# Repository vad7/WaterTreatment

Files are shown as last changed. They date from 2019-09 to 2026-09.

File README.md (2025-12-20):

# Контроллер водоподготовки и водоснабжения
Для контроллера используется плата Arduino DUE или Arduino DUE Core (ARM SAM3x8e).<br>

Также, как минимум, нужны платы: реле, часов DS3231 + EEPROM, сети на W5500.<br>
Детальное описание: http://vad-7.blogspot.com/2019/12/blog-post.html <br>
<br>
Возможности (версия 1.1.72):<br>
* Управление дозатором реагента по расходу
* Промывка двух фильтров (например - обезжелезивателя, умягчителя) по времени и по расходу<br>
* Управление насосной станцией по датчику давления воды, защита от перегрузки и сухого хода<br>
* Глубокий контроль рабочего состояния системы
* Графический веб-интерфейс с поддержкой мобильных устройств<br>
* Текстовый дисплей LCD2004, кнопки управления<br>
* Расширенная статистика с записью на SD карту<br>
* Оповещения о сбоях через email или sms.<br>
* Modbus RTU - Счетчик электричества (PZEM-004Tv3/PZEM-0xx), платы Реле. Автовыбор портов 1-3<br>
* Весы на плате HX711 для контроля уровня реагента<br>
* Аналоговый датчик уровня воды 4-20 mA<br>
* Датчик температуры DS18B20 или NTC<br>
* Контроль протечек (датчики XKC-Y25), затопления (датчики типа поплавок), переполнения бака<br>
* Контроль работы дренажного насоса (вторая шина Modbus-RTU), с возможностью отключения через Modbus реле, защита от сухого хода и перегрузки<br>
* Возможность подключения счетчика питьевого фильтра (обратного осмоса)<br>
* Управление подогревом септика<br>
* Контроль насоса откачки септика, реле насоса септика, возможность работы со сломаным поплавком или без поплавка<br>
* Другая автоматизация (например, вентилирование газов - радона и сероводорода, слив осадка бака)<br>
* Расширенный контроль безопасности (сухой ход и перегрузка НС, незакрытый кран, забитый инжектор и т.п.)<br>
* Датчик протока (FS-K2) фильтра питевой воды (обратный осмос), поддержка повышенного давления воды при заполнении ОС фильтра
* Таймеры (ежесуточные и периодические), включение обычных реле и Modbus

<br>

Схема
Схема_2
Датчики
Плата

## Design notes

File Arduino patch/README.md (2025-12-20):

# WaterTreatment
Файлы которые надо заменить в стандартном SDK Due (смотрите путь к файлам начиная с hardware)<br>
Папку "sam" перезаписать скорее всего куда-то сюда: "C:\Users\\%USERNAME%\AppData\Local\Arduino15\packages\arduino\hardware\\"<br>
Библиотека DUE SAM: https://github.com/arduino/ArduinoCore-sam

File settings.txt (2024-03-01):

 ------ Контроллер водоподготовки ver. 1.51  сборка Feb 17 2024 14:24:27 ------
Конфигурация: vad7: Водоснабжение, Обезжелезивание Quantum DMI-65, Дозирование хлора, Умягчение
Создание файла: 09:28:39 19.02.2024 

  1.1 Опции
 - Настройка встроенных графиков -
Период накопления графиков (сек): 10
Запись графиков на карту памяти: 1
 - Дополнительное оборудование -
Логировать обмен между беспроводными датчиками: 0
Генерация звукового сигнала: 1
На шинах 1-Wire(DS2482) только один датчик: 1 

  1.2 Сетевые настройки
Использование DHCP: 0
IP адрес контроллера: 192.168.0.8
DNS сервер: 8.8.8.8
Шлюз: 192.168.0.1
Маска подсети: 255.255.255.0
MAC адрес контроллера: DE:A1:1E:01:02:04
Запрет пинга контроллера: 0
Использование паролей: 1
Пароль пользователя (user): 
Пароль администратора (admin): q12
Проверка ping до сервера: never:0;1 min:0;5 min:0;20 min:0;60 min:1;120 min:0;
Адрес пингуемого сервера: 192.168.0.1
Ежеминутный контроль связи с Wiznet W5xxx: 1
Время очистки сокетов: never:0;10 sec:0;30 sec:1;90 sec:0;
Время сброса чипа: W5500: never:1;6 hours:0;24 hours:0;
Размер пакета для отправки в байтах: 1465
Не ожидать получения ACK при посылке следующего пакета: 0
Пауза перед отправкой следующего пакета, если нет ожидания ACK. (мсек): 10

  1.3 Настройки даты и времени
Установленная дата: 19.02.2024
Установленное время: 09:28
Адрес NTP сервера: ntp0.ntp-servers.net
Часовой пояс (часы): 3
Синхронизация времени по NTP раз в сутки: 1
Синхронизация раз в час с I2C часами: 0

  1.4 Уведомления
Сброс контроллера: 1
Возникновение ошибок: 1
Сигнал «жизни» (ежедневно в 12-00): 0
Достижение граничной температуры: 1
 Граничная температура в доме (если меньше то посылается уведомление): 2.00
Проблемы с SD картой и SPI flash: 1
Прочие уведомления: 1
 - Настройка отправки почты -
Посылать уведомления по почте: 1
Адрес smtp сервера: mail.smtp2go.com
Порт smtp сервера: 25
Необходимость авторизации на сервере: 1
Логин для входа: Arduino-DUE
Пароль для входа: ...
Адрес отправителя: ...
Адрес получателя: ...
Добавлять в уведомление информацию о состоянии: 1
 - Настройка отправки SMS -
Посылать уведомления по SMS: 0
Телефон получателя: 0.380
Сервис отправки SMS: sms.ru:1;smsc.ru:0;smsc.ua:0;smsclub.mobi:0;
Адрес сервиса отправки SMS: 0.0.0.0
API ID: api_id
none: none

  1.5 Настройка MQTT
Не поддерживается, нет в прошивке
  2.1 Датчики температуры
AIR     [28FFF949621403B1] Температура воздуха:  T=11.18, Tmin=1.00, Tmax=30.00, Terr=0.00, Ttest=12.00

  2.2 Аналоговые датчики
PWATER  Датчик давления воды:  P=2.87 Pmin=2.50 Pmax=3.80 Ptest=3.00 Zero=40 Kof=0.175 Pin=AD10
LTANK   Датчик уровня бака:  P=97.29 Pmin=5.00 Pmax=99.00 Ptest=8.90 Zero=4005 Kof=4.500 Pin=AD1

  2.3 Датчики сухой контакт
REG     Идет регенерация:  In=0 Level=0 Test=0 Pin=56 Type=
REGBW   Идет обратная промывка:  In=0 Level=0 Test=0 Pin=43 Type=
REG2    Идет регенерация умягчителя:  In=0 Level=0 Test=0 Pin=54 Type=
FLOOD   Затопление:  In=0 Level=1 Test=0 Pin=23 Type=
LEAK    Протечка:  In=0 Level=1 Test=0 Pin=24 Type=
SEPTIC  Авария септика:  In=0 Level=1 Test=0 Pin=5 Type=

  3.1 Реле
RBST1   Реле насосной станции Pin:47 Status: 0
RBST2   Реле насосной станции 2 Pin:3 Status: 0
RFEEDP  Реле включения дозирующего насоса Pin:46 Status: 0
RWON    Реле подачи воды Pin:7 Status: 1
RWOFF1  Реле отключения воды после фил.1 Pin:45 Status: 0
RSTREG  Реле старта рег. обезжелезивателя Pin:9 Status: 0
RSTREG2 Реле старта рег. умягчителя Pin:8 Status: 0
RDRAIN  Реле слива 1 Pin:44 Status: 0
RDRAIN2 Реле слива 2 Pin:6 Status: 0
RFILL   Реле заполнения бака Pin:31 Status: 0
RSILT   Реле слива отстоя бака Pin:50 Status: 0

  3.1 Реле
RBST1   Реле насосной станции Pin:47 Status: 0
RBST2   Реле насосной станции 2 Pin:3 Status: 0
RFEEDP  Реле включения дозирующего насоса Pin:46 Status: 0
RWON    Реле подачи воды Pin:7 Status: 1
RWOFF1  Реле отключения воды после фил.1 Pin:45 Status: 0
RSTREG  Реле старта рег. обезжелезивателя Pin:9 Status: 0
RSTREG2 Реле старта рег. умягчителя Pin:8 Status: 0
RDRAIN  Реле слива 1 Pin:44 Status: 0
RDRAIN2 Реле слива 2 Pin:6 Status: 0
RFILL   Реле заполнения бака Pin:31 Status: 0
RSILT   Реле слива отстоя бака Pin:50 Status: 0

  3.5. Частотные датчики потока
FLOW    Датчик протока:  Контроль мин. потока: 0, Минимальный поток (куб/ч)=0.000, Коэффициент (имп*л)=400.000, Тест (куб/ч)=0.000

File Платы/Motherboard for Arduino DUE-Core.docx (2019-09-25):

Платы 100x100мм.

Главная плата питается от 5V. Для аналогового выхода есть возможность подключить другое напряжение.

На плате места для:

1. платы часов (ZS_042)

2. платы сети W5500 lite (USR-ES1)

3. платы MicroSD 5V

4. разъем MicroSD

5. 3-х узких плат RS485 - TTL или других Serial-устройств.

6. 2 платы для датчиков температуры DS18B20 или других I2C устройств

7. дисплея LCD2004 (1602)

8. 4-х кнопок

9. Вторая шина I2C.

Входы-выходы:

1. два токовых входа (4-20 мА)

2. три аналоговых входа с подстройкой

3. два аналоговых выхода (LM358)

4. 18 цифровых выходов, включая 7 от ULN2003 для ЭРВ

5. 6 цифровых входов

6. Выход 5V через транзистор для пищалки, сирены или т. п.

Клеммники с шагом 5мм (KF128/129-5.08), на пищалку с шагом 3.5мм (KF350-3.5)

Плата реле реле подключается 20 пиновым двурядным шлейфом с шагом 2.54 мм (JTAG 2.54mm 20 pin).

На плату подается с внешнего источника высокое напряжение (12-24V и/или 5V) от них питаются ULN и реле.

На плате:

1. 6 развязанных через оптрон цифровых входа (клеммник KF350-3.5)

2. 5 твердотельных реле: оптосимистор + симистор BTA16 (16A), один можно воткнуть BTA41 (41A). (KF129-5.08)

3. 1 обычное реле на 16A, переключающие контакты (Omron G2RL-1-E или аналог) (KF129-5.08)

4. два выхода через оптрон, один можно сделать аналоговым через PWM. (KF350-3.5)

5. ULN2003 для управления ЭРВ или типа того (KF350-3.5)

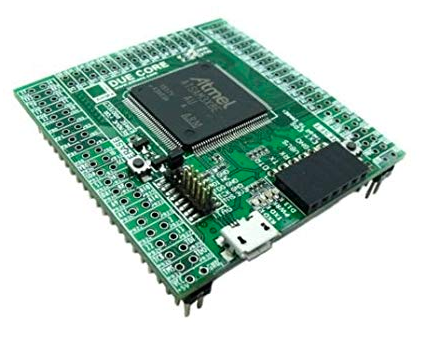
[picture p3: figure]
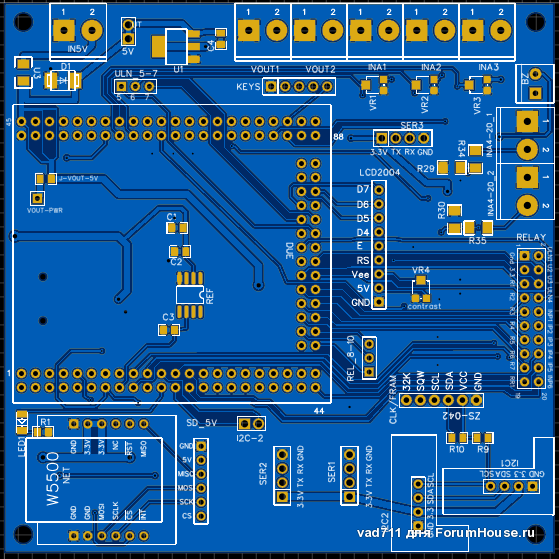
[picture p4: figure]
attachFull6571619

Плата реле:

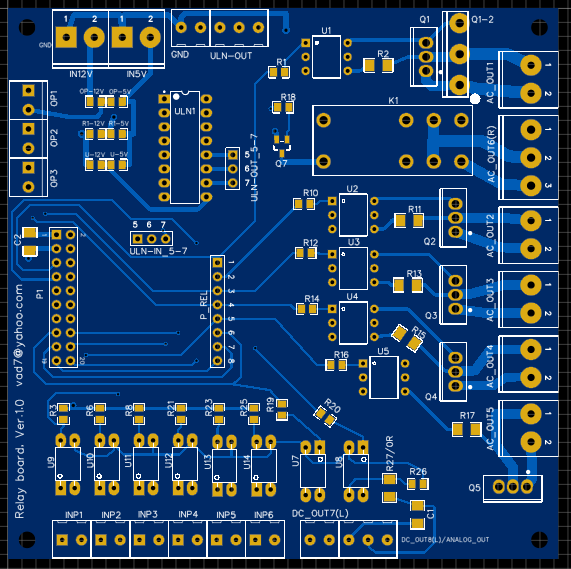
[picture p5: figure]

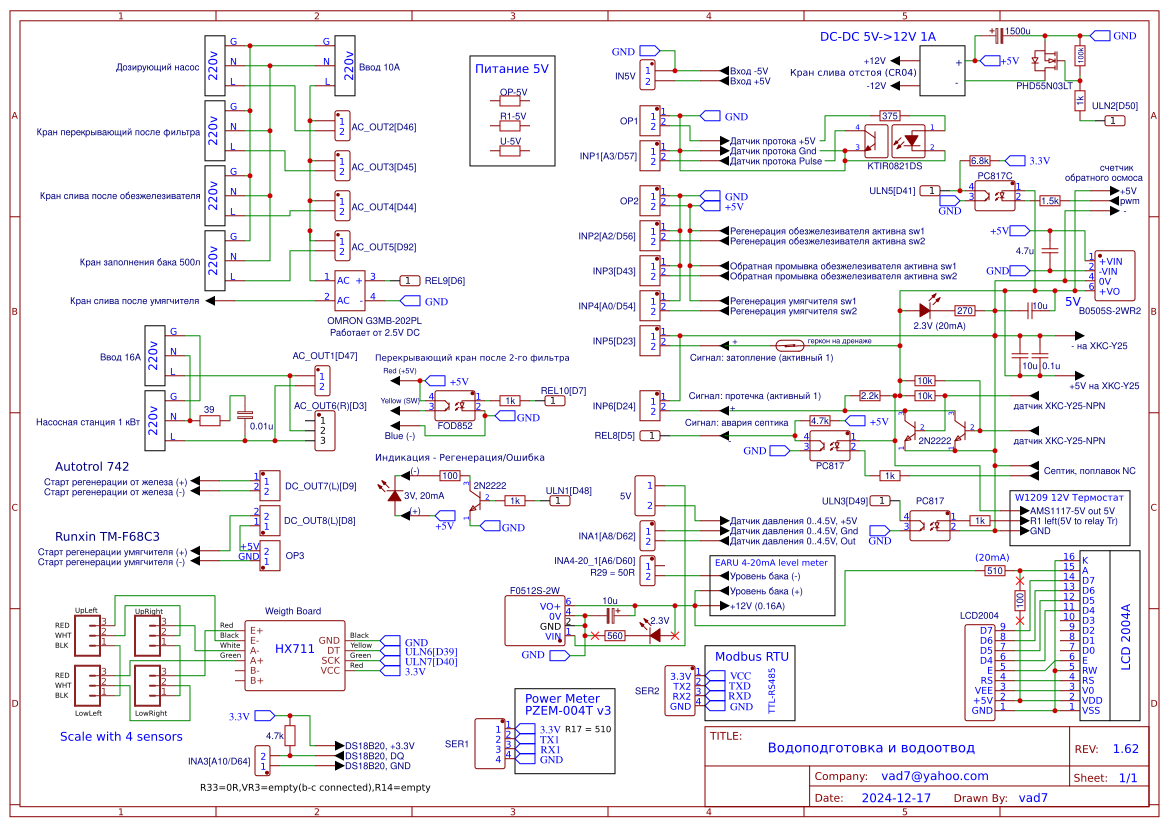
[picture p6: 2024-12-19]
Schematic_Water-Treatment_Sheet-1.png

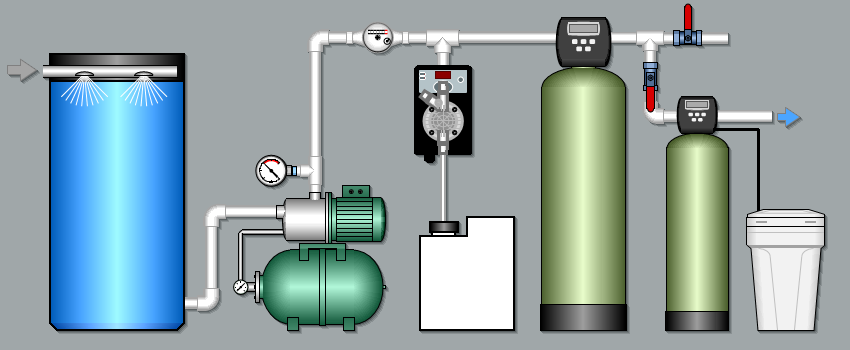
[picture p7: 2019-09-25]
Pics/plan 3.png

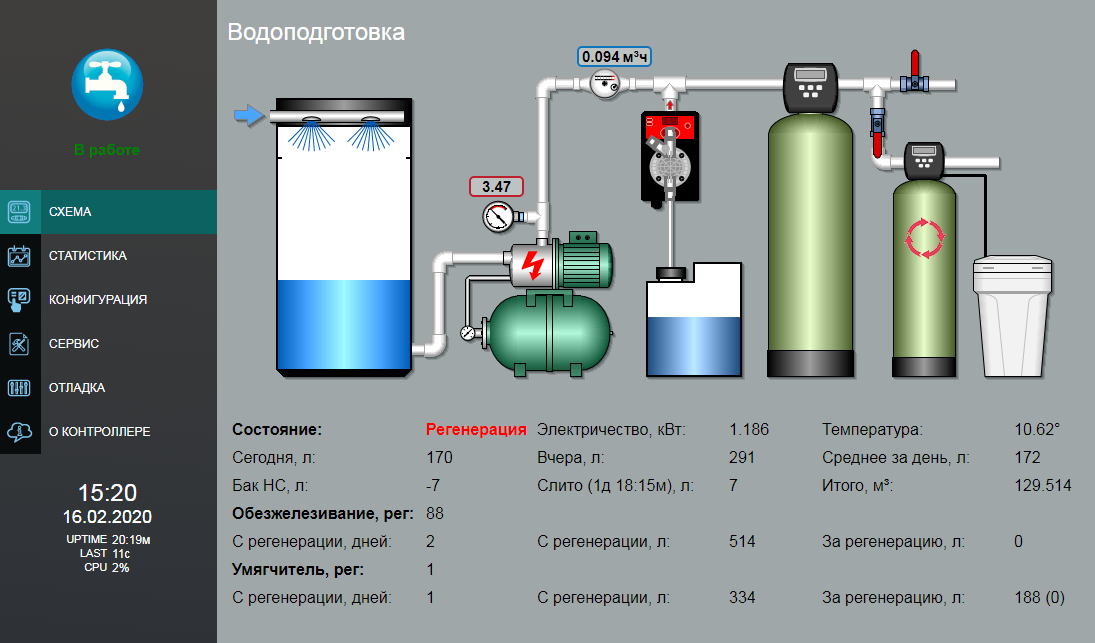
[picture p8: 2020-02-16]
Screenshoot_2.png

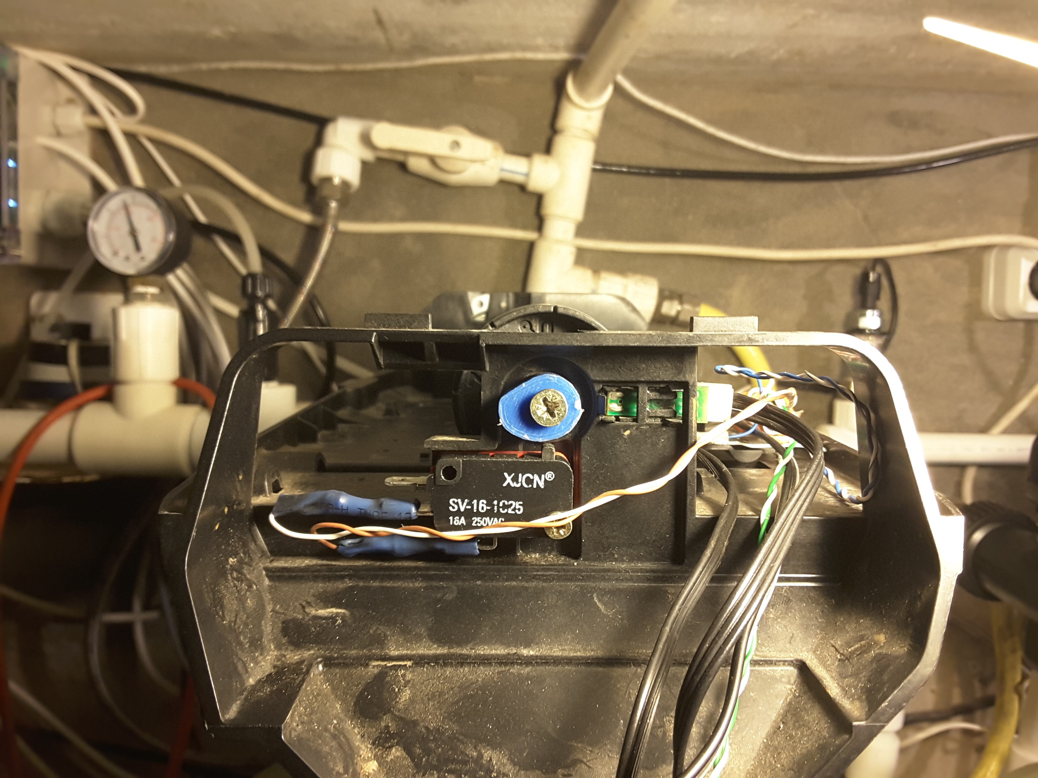
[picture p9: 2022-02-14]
Pics/FilterSwitch.jpg

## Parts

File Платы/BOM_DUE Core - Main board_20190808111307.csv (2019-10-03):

ID | Name | Designator | Footprint | Quantity | Manufacturer Part | Manufacturer | Supplier | Supplier Part | LCSC Assembly | SeeedStudio
1 | W5500 module | NET | W5500_MODULE | 1 | ?
2 | ZS_042/DS3231 | CLK/FRAM | ZS-042 | 1 | DS3231
3 | ADR4530BRZ | REF | SOIC-8_150MIL | 1 | ADR4530BRZ | Analog Devices | LCSC | C208042
4 | 1u | C1 | 0805' | 1 | ?
5 | 0.1u | C2,C3,C4,C5,C9 | 0805' | 5 | ?
6 | Serail1 | SER1,SER2,SER3 | DIP-1X4P-2.54MM RS485-UART | 3 | 210S-1*4P L=11.6MMGold-plated black | Ckmtw | LCSC | C124378
7 | (3.3V) | I2C1,I2C2 | HDR-4X1/2.54 I2C BOARD | 2 | Headers Pins 1*4P | ReliaPro | LCSC
8 | LM1117-3.3 | U1 | SOT-223 | 1 | LM1117IMPX-3.3/NOPB | TI | LCSC | C23984 | Yes
9 | 10u | C6 | 0805' | 1 | ?
10 | LED GREEN | LED1 | LED-1206F | 1 | 15-21/RSC-BS1T2B/2T | Everlight Elec | LCSC | C264385
11 | 330 | R1 | 0805' | 1 | ?
12 | 10к | R2 | 0805' | 1 | ?
13 | 10k | R3,R4,R9,R10 | 0805' | 4 | ?
14 | 10u | C7,C8 | 1206 | 2 | ?
15 | 22.1k | R5,R6 | 0805' | 2 | ?
16 | 9.09k | R7,R8 | 0805' | 2 | ?
17 | KF128_2P_5.08 | VOUT1,VOUT2,IN5V | KF128_2P_5.08 | 3 | KF128L-5.08 | Kefa Electronics
18 | BC817 | Q6 | SOT-23(SOT-23-3) | 1 | BC817 | CJ | LCSC | C8589 | Yes
19 | 100 | R29,R30 | 1206 | 2 | ?
20 | BAT54S | D2,D4,D5,D6,D3 | SOT-23(SOT-23-3) | 5 | BAT54S | SEMTECH | LCSC | C83935 | Yes
21 | 0.01u | C10,C12,C13,C14,C11 | 0805' | 5 | ?
22 | 10K | VR1,VR2,VR3,VR4 | RES-ADJ-SMD_3PIN-V-L3.1-W3.8-H1.62-PITCH1.0 | 4 | EVM3ESX50B14 | PANASONIC | LCSC | C11959
23 | 6.8k | R32,R31,R33 | 0805' | 3 | ?
24 | 0R | R34,R35 | 1206 | 2 | ?
25 | Header-Male-2.54_2x10 | RELAY | HDR-10X2/2.54 | 1 | ? |  | LCSC | C62032
26 | KF301-2P | INA4-20_1,INA4-20_2,INA1,INA2,INA3 | KF128_2P_5.08 | 5 | ? |  | LCSC | C8445
27 | Header-Male-2.54_1x3 | ULN_5-7,REL_8-10,DAC0 | HDR-3X1/2.54 | 3 | Header2.54mm 1*3P | BOOMELE | LCSC | C49257
28 | 0R | J-VOUT-5V | 0805' | 1 | ?
29 | Header-Male-2.54_1x1 | VOUT-PWR | HDR-1X1/2.54 | 1 | Header-Male-2.54_1x1 | ReliaPro | LCSC | C81276
30 | MicroSD board | SD_5V | MICROSD CARD ADAPTER | 1 | ? |  | Hernan
31 | SMBJ5.0A | D1 | SMB/DO-214AA | 1 | SMBJ5.0A | Brightking | LCSC | C78423 | Yes
32 | CC12H2A-TR | U3 | FUSE-CC12H | 1 | CC12H2A-TR | BUSSMANN | LCSC | C340908
33 | Header-Male-2.54_1x2 | 5V | HDR-2X1/2.54 | 1 | 826629-2 | TE Connectivity | LCSC | C86471
34 | MicroSD socket SPI | MICROSD | MICROSD SOCKET | 1 | ?
35 | LCD 1602, 2004. 4-bit mode (HD44780) pin-header | LCD2004 | HDR-16X1/2.54 - LCD1602, LCD2004 | 1 | 16x2 LCD (HD44780)
36 | Arduino Due-Core | DUE | ARDUINO DUE CORE | 1 | ? |  |  | undefined
37 | 2.54mm 1*2P | I2C-2 | HDR-2X1/2.54 | 1 | 2.54mm 1*2P | ReliaPro | LCSC | C36717
38 | Buzzer | BZ | KF350-3.5MM-2P | 1 | WJ2EDGVC-5.08-2P | ReliaPro | LCSC | C8445
39 | Header-Male-2.54_1x5 | KEYS | DIP-1X5P-2.54MM-M | 1 | 210S-1*5P L=11.6MMGold-plated black | Ckmtw | LCSC | C124379
40 | LM358DR | U2 | SOIC-8_150MIL | 1 | LM358DR | TI | LCSC | C5423 |  | 310020021

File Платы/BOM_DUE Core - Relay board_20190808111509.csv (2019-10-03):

ID | Name | Designator | Footprint | Quantity | Manufacturer Part | Manufacturer | Supplier | Supplier Part | _Price | LCSC Assembly | EasyEDA
1 | 330 | R10,R12,R14,R1 | 0805' | 4 | ?
2 | 51 | R11,R13,R15,R17,R2 | 1206 | 5 | ?
3 | MOC3063 | U2,U3,U4,U5,U1 | DIP6 | 5 | ?
4 | BTA16-600CW | Q2,Q3,Q4,Q5,Q1 | TO-220(TO-220-3) | 5 | BTA16-600CWRG | STMicroelectronics | LCSC | C84597
5 | 680 | R16 | 0805' | 1 | ?
6 | G2RL-1-E-5VDC | K1 | G2RL-1-E-CN DC24 | 1 | - | Omron Electronics | LCSC | C231363
7 | SS18 | D1 | SMA(DO-214AC) | 1 | SS18 | MDD | LCSC | C64986 |  | Yes
8 | BC817 | Q7 | SOT-23(SOT-23-3) | 1 | BC817 | CJ | LCSC | C8589 |  | Yes
9 | 10k | R18 | 0805' | 1 | ?
10 | 1k | R19,R20,R4,R5,R7,R9,R22,R24 | 0805' | 8 | ?
11 | FOD852/PC817/TLP126 | U7,U8 | PC817-DIP/SMD | 2 | FOD852SD | ON Semicon | LCSC | C258252 |  | Yes
12 | ULN2003AN | ULN1 | DIP-16_16PIN-LS7.62-L19.69-W6.6-H5.08-PITCH2.54 | 1 | ULN2003AN | TI | LCSC | C90448
13 | Header-Male-2.54_1x8 with numbers | P_REL | HDR-8X1/2.54 | 1 | Header-Male-2.54_1x8 | EasyEDA | EasyEDA | E49256 |  |  | E49256
14 | Header-Male-2.54_2x10 | P1 | HDR-10X2/2.54 | 1 | ? |  | LCSC | C62032
15 | PC817/TLP126/HCPL814 | U9 | PC817-DIP/SMD | 1 | FOD852SD | ON Semicon | LCSC | C258252 |  | Yes
16 | 4.7k | R3,R6,R8,R21,R23,R25,R26 | 0805' | 7 | ?
17 | PC817/TLP126 | U10,U11,U12,U13,U14 | PC817-DIP/SMD | 5 | FOD852SD | ON Semicon | LCSC | C258252 |  | Yes
18 | 0 | OP-12V,OP-5V,R1-5V,R1-12V,U-12V,U-5V | 0805' | 6 | ?
19 | KF128_2P_5.08 | IN12V,IN5V | KF128_2P_5.08 | 2 | KF128L-5.08 | Kefa Electronics
20 | 20k | R27 | 1206 | 1 | ?
21 | 10u | C1,C2,C3,C4 | 1206 | 4 | ?
22 | KF129_2P_5.08 | AC_OUT5,AC_OUT4,AC_OUT3,AC_OUT2,AC_OUT1 | KF129_2P_5.08 | 5 | KF129L-5.08 | Kefa Electronics |  | undefined
23 | Header-Male-2.54_1x3 | ULN-IN_5-7,ULN-OUT_5-7 | HDR-3X1/2.54 | 2 | Header2.54mm 1*3P | BOOMELE | LCSC | C49257
24 | KF129_3P_5.08 | AC_OUT6(R) | KF129_3P_5.08 | 1 | ? | Molex
25 | BTA41 | Q1-2 | TOP3-1 | 1 | BTA41-600BRG | STMicroelectronics | LCSC | C9103
26 | KF350-3P | DC_OUT8(L)/ANALOG_OUT,ULN-OUT | KF350-3P | 2 | WJ2EDGK-5.08-3P-14-00A | ReliaPro | LCSC | C71371
27 | KF350-3.5mm-2p | OP1,OP2,OP3 | KF350-3.5MM-2P | 3 | WJ2EDGVC-5.08-2P | ReliaPro | LCSC | C8445
28 | KF350-3.5mm-2p | DC_OUT7(L),GND,INP1,INP2,INP3,INP4,INP5,INP6 | KF350-2P | 8 | WJ2EDGVC-5.08-2P | ReliaPro | LCSC | C8445
29 | 0.1u | C5 | 1206 | 1 | ?

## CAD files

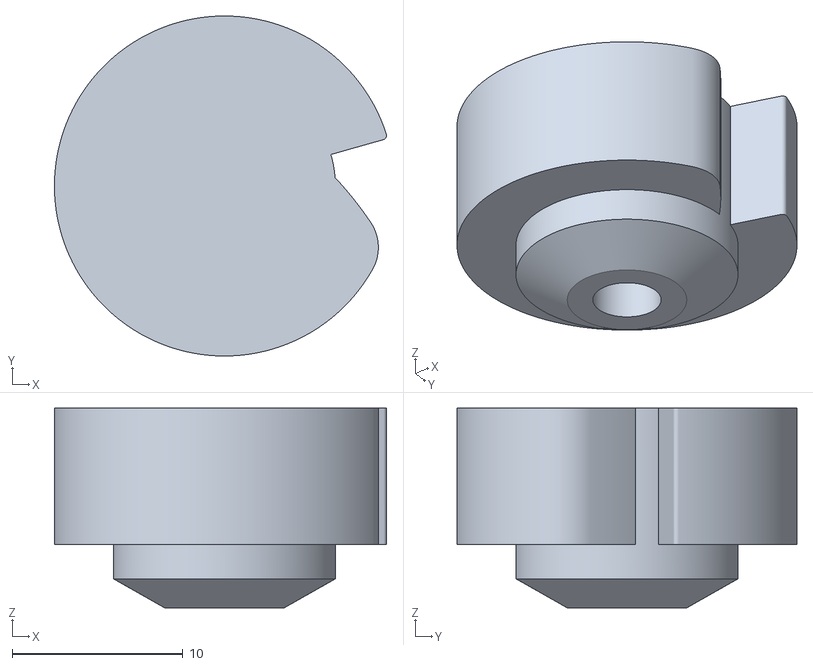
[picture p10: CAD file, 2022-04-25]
Microswitch_cam_Autotrol_263-268_softener3.stl
19.5 x 19.9 x 11.7

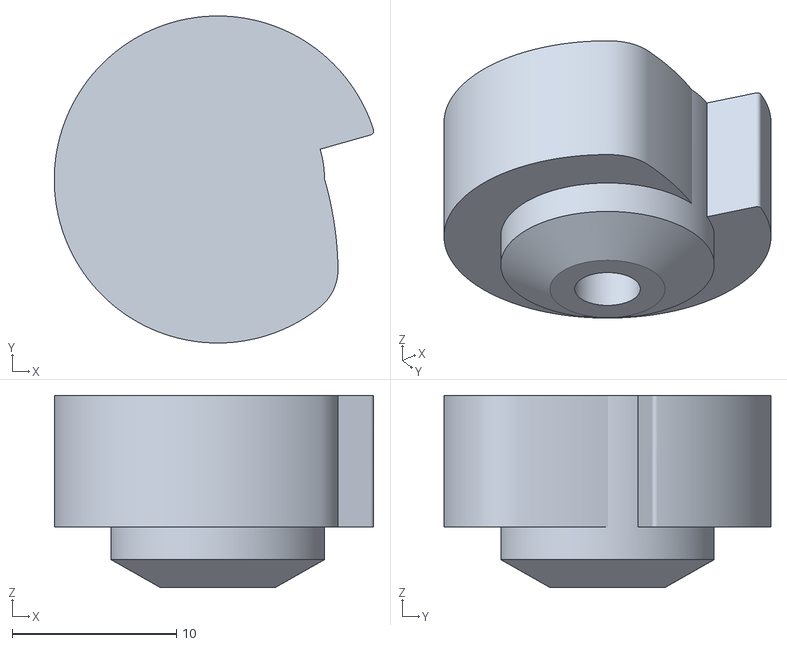
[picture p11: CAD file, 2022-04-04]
Microswitch_cam_Autotrol_263-268_softener2.stl
19.5 x 19.9 x 11.7

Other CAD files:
Microswitch_cam_Autotrol_263-268_softener.stl

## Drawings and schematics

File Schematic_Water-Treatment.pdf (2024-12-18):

## Питание 5V

## DC-DC 5V->12V 1A

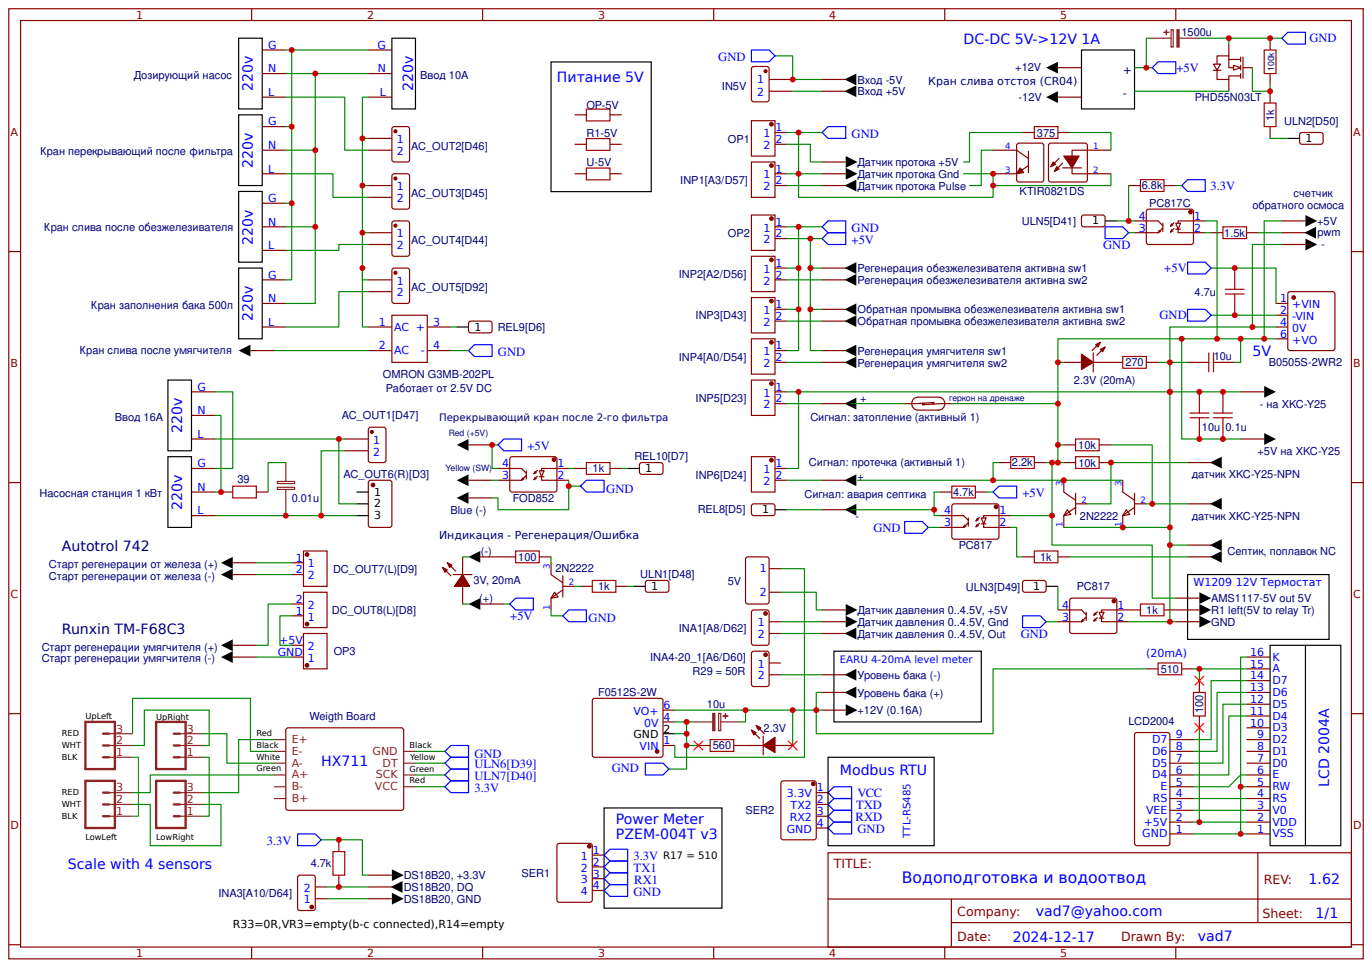
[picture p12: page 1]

Кран перекрывающий после фильтра

Кран слива после обезжелезивателя

Обратная промывка обезжелезивателя активна sw1
Обратная промывка обезжелезивателя активна sw2

Перекрывающий кран после 2-го фильтра

Старт регенерации от железа (+)
Старт регенерации от железа (-)

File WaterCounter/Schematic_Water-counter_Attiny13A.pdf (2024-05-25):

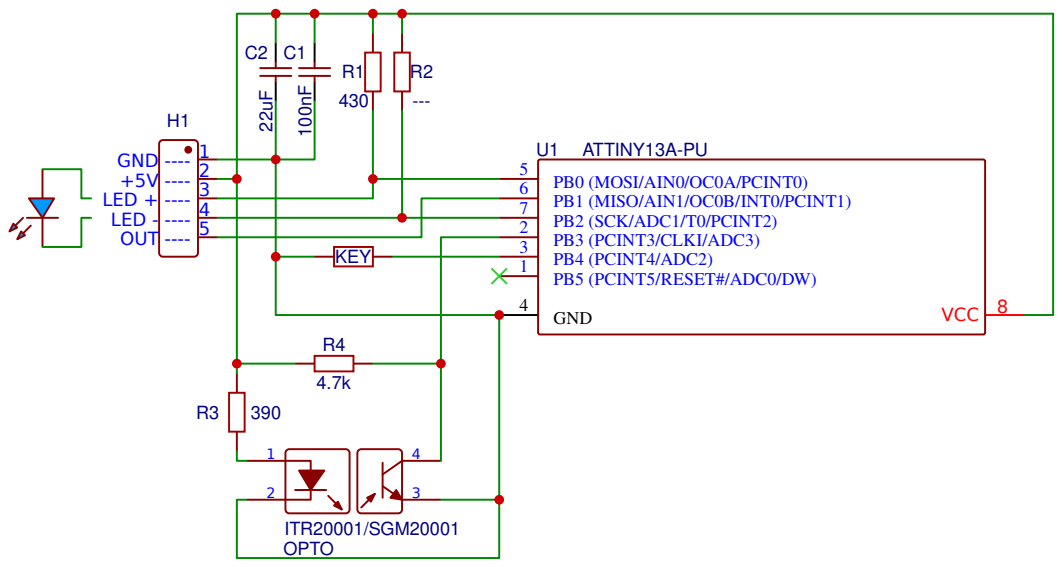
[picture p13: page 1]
TITLE:; Water counter, pulse out only; REV: 1.0; Date:; Sheet: 1/1; Drawn By: vad7; ATTINY13A-PUU1; PB5 (PCINT5/RESET#/ADC0/DW); PB3 (PCINT3/CLKI/ADC3); PB4 (PCINT4/ADC2); GND; PB0 (MOSI/AIN0/OC0A/PCINT0); PB1 (MISO/AIN1/OC0B/INT0/PCINT1); PB2 (SCK/ADC1/T0/PCINT2); VCC 8; ITR20001/SGM20001 OPTO; H1 GND ---- 1 +5V ---- 2 LED + ---- 3 LED - ---- 4 OUT ---- 5; KEY

Company: vad7@yahoo.com

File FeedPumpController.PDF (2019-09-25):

J2

VS2

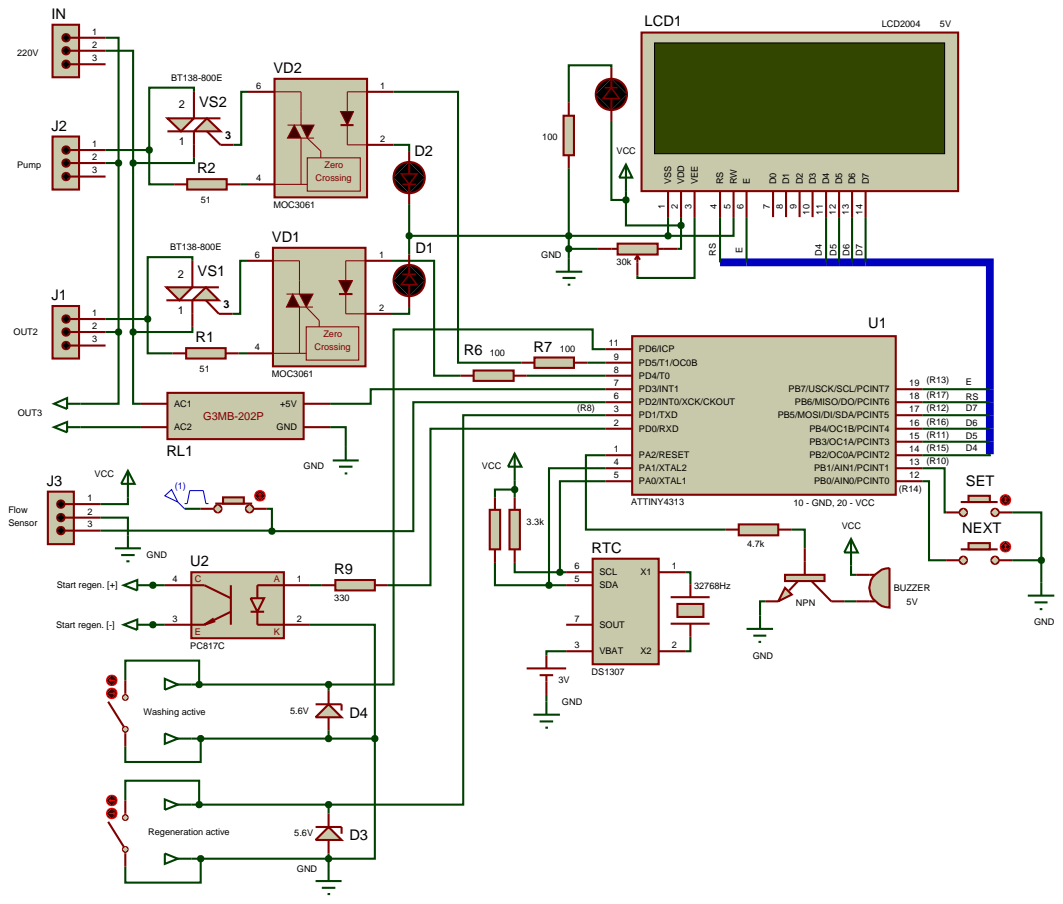
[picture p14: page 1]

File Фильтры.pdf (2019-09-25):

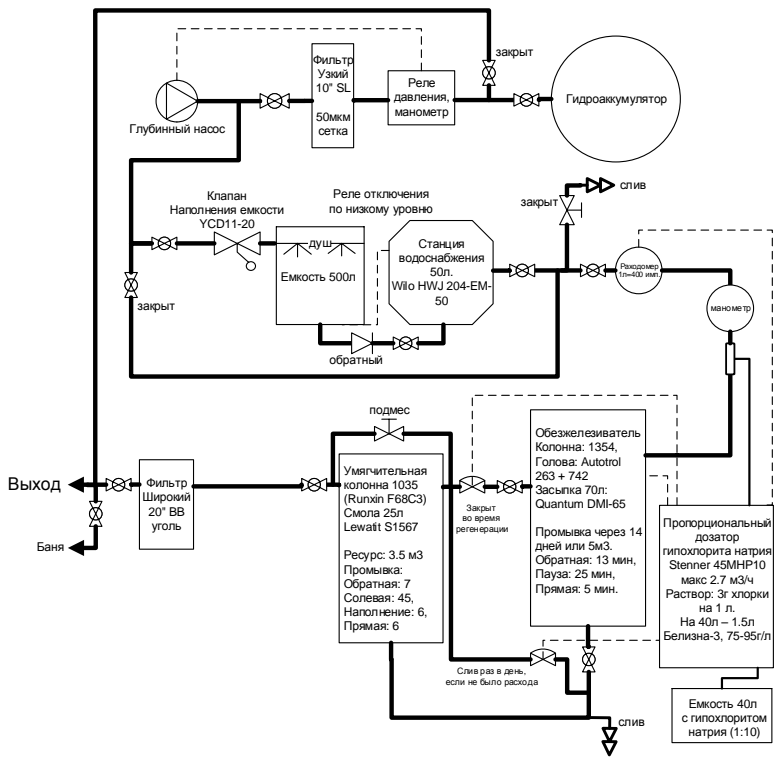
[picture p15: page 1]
Глубинный насос; Гидроаккумулятор; Фильтр Узкий 10" SL; 50мкм сетка; Реле давления, манометр; Станция водоснабжения 50л.; Умягчительная колонна 1035 (Runxin F68C3) Смола 25л Lewatit S1567; Ресурс: 3.5 м3 Промывка: Обратная: 7 Солевая: 45, Наполнение: 6, Прямая: 6; Обезжелезиватель Колонна: 1354, Голова: Autotrol 263 + 742 Засыпка 70л: Quantum DMI-65; Промывка через 14 дней или 5м3. Обратная: 13 мин, Пауза: 25 мин, Прямая: 5 мин.; Фильтр Широкий 20" BB уголь; Выход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

Реле отключения
по низкому уровню

Wilo HWJ 204-EM-

Слив раз в день,
если не было расхода

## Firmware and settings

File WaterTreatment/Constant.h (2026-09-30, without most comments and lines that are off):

#define Constant_h
#include "Config.h"                         // Цепляем сразу конфигурацию
#include "Util.h"
#define VERSION			  "1.84"			// Версия прошивки
#define VER_SAVE		  16				// Версия формата сохраняемых данных в I2C память
#define FAST_LIB                            // использование допиленной библиотеки езернета
#define TIME_ZONE         3                 // поправка на часовой пояс по ДЕФОЛТУ
#define NTP_SERVER        "time.nist.gov"   // NTP сервер для синхронизации времени по ДЕФОЛТУ
#define NTP_SERVER_LEN    60                // максимальная длиная адреса NTP сервера
#define NTP_PORT		  123
#define NTP_LOCAL_PORT    8888              // локальный порт, который будет прослушиваться на предмет UDP-пакетов NTP сервера
#define NTP_REPEAT        3                 // Число попыток запросов NTP сервера
#define NTP_REPEAT_TIME   1000              // (мсек) Время между повторами ntp пакетов
#define PING_SERVER       "8.8.8.8"         // ping сервер по ДЕФОЛТУ
#define WDT_TIME          6                 // период Watchdog таймера секунды но не более 16 секунд!!! ЕСЛИ установить 0 то Watchdog будет отключен!!!
#define INDEX_FILE        "index.html"       // стартовый файл по умолчанию для большой морды
#define INDEX_MOB_FILE    INDEX_FILE         // стартовый файл по умолчанию для мобильной морды
#define HEADER_BIN        "WT-SAVE-DATA"    // Заголовок (начало) файла при сохранении настроек. Необходим для поиска данных в буфере данных при восстановлении из файла
#define MAX_LEN_PM        250               // максимальная длина строкового параметра в запросе (расписание бойлера 175 байт) кодирование описания профиля 40 букв одна буква 6 байт (двойное кодирование)
#define CHART_POINTS       300               // Максимальное число точек графика, одна точка это 2 байта * число графиков
#define ADC_PRESCAL       2					// ADCClock = MCK / ( (PRESCAL+1) * 2 )
byte defaultMAC[] = { 0xDE, 0xA1, 0x1E, 0x01, 0x02, 0x04 };// не менять
const uint16_t  defaultPort=80;
#define GETBIT(b,f)   ((b&(1<<(f)))?true:false)              // получить состяние бита
#define SETBIT1(b,f)  (b|=(1<<(f)))                          // установка бита в 1
#define SETBIT0(b,f)  (b&=~(1<<(f)))                         // установка бита в 0
#define ALIGN(a) ((a + 3) & ~3)
#define SD_REPEAT         3                 // Число попыток чтения карты, открытия файлов, при неудаче переход на работу без карты
#define W5200_THREAD      3                 // Число потоков для сетевого чипа w5200 допустимо 1-4 потока, на 4 скорее всего не хватить места в оперативке
#define W5200_NUM_PING    4                 // Число попыток пинга до определения потери связи
#define W5200_TIME_PING   1000              // мсек Время между попытками пинга (если не удача)
#define W5200_MAX_LEN     2048 //=W5100.SSIZE // Максимальная длина буфера, определяется W5200 не более 2048 байт
#define W5200_NUM_LINK    2                 // Число попыток сброса чипа w5500 и проверки появления связи (кабель воткнут) используется для инициализаци чипа
#define W5200_TIME_LINK   4000              // Максимальное время ожидания устанoвления связи (поднятие Link) кабель воткнут  используется для инициализаци чипа (мсек)
#define W5200_TIME_WAIT   3000              // Время ожидания захвата мютекса (переключение потоков) мсек
#define W5200_TIME_WAIT_MAX (10*60*1000UL)	// Время ожидания захвата макс
#define W5200_SPI_SPEED   SPI_RATE          // ЭТО ДЕЛИТЕЛЬ (SPI_RATE определен в w5100.h)!!! Частота SPI w5200 = 84/W5200_SPI_SPEED т.е. 2-42МГц 3-28МГц 4-21МГц 6-14МГц Диапазон 2-6
#define W5200_SOCK_SYS    (MAX_SOCK_NUM-1)  // Номер системного сокета который не использутся в вебсервере, это последний сокет, НЕ МЕНЯТЬ
#define W5200_RTR         (2*0x07D0)        // время таймаута в 100 мкс интервалах  (по умолчанию 200ms(100us X 2000(0x07D0))) актуально для комманд CONNECT, DISCON, CLOSE, SEND, SEND_MAC, SEND_KEEP
#define W5200_RCR         (0x04)            // число повторов передачи  (по умолчанию 0x08 раз))
#define MAIN_WEB_TASK      0                // какой поток вебсервера является основным (поток в котором идет отправка MQTT и уведомлений) обычно 0
#define W5500_LINK_CHECK  30				// Периодичность контроля соединения, сек
#ifdef DEBUG_NATIVE_USB
	#define SerialDbg	SerialUSB
#else
	#define SerialDbg	Serial
#endif
#if RADIO_SENSORS_PORT == 2
	#define RADIO_SENSORS_SERIAL	Serial2	// Аппаратный порт
#elif RADIO_SENSORS_PORT == 3
	#define RADIO_SENSORS_SERIAL	Serial3	// Аппаратный порт
#endif
#define RADIO_LOST_TIMEOUT 30*60*1000		// через сколько считать, что связь потеряна с датчиком, мсек
#define cDELAY_DS1820         750            // мсек. Задержка для чтения DS1820 (время преобразования)
#define TIME_READ_SENSOR      4000		     // мсек. Период опроса датчиков
#define TIME_WEB_SERVER       2              // мсек. Период опроса web_server()
#define TIME_I2C_UPDATE       (60*60)*1000   // мсек. Время обновления внутренних часов по I2С часам (если конечно нужно)
#define TIME_MESSAGE_TEMP     300			 // 1/10 секунды, Проверка граничных температур для уведомлений
#define TIME_LED_OK           1500UL         // Период мигания светодиода при ОК (мсек)
#define TIME_LED_ERR          200            // Период мигания светодиода при ошибке (мсек).
#define TIME_BEEP_ERR         2000UL         // Период звукового сигнала при ошибке, мсек
#define cDELAY_START_MESSAGE  60             // Задержка (сек) после старта на отправку сообщений
#define cDELAY_REPEAT_MESSAGE 300            // Повтораня попытка отправки email через сек
#define NO_POWER_ON_DELAY     15		     // Задержка включения после появления питания, сек
#define WB_LOW_CONSUME_MAX_TIME 25000		 // Максимальное время бесперерывной работы насосной станции. После него будет переыв на включение дозатора, ms
#define WEB0_OTHER_FUNC_PERIOD 10            // Период выполнения других функция в задаче Web0, сек
#define DISPLAY_UPDATE		  2500           // Время обновления информации на дисплее (мсек)
#define KEY_CHECK_PERIOD	  10             // ms
#define KEY_DEBOUNCE_TIME	  50             // ms
#define DISPLAY_SETUP_TIMEOUT 600000         // ms
#define TIMER_TO_SHOW_STATUS  2500			// мсек, Время показа активного состояния (дозирующего насоса, ...)
#define HTTP_REQ_LowConsume   60  			// s, Период запроса о работе от резервного источника, по умолчанию
#define HTTP_REQ_TIMEOUT      2000			// ms
#define HOUR_SIGNAL_LIFE      12            // Час когда генерится сигнал жизни
#define NIGHT_END_HOUR			7			// Час после ночного тарифа
#define LCD_COLS			20			// Колонок на LCD экране
#define LCD_ROWS			4			// Строк на LCD экране
#define MAX_TEMP_ERR		700         // Максимальная систематическая ошибка датчика температуры (сотые градуса)
#define NUM_READ_TEMP_ERR	10          // Число ошибок подряд чтения датчика температуры после которого считается что датчик не исправен
#define RES_ONEWIRE_ERR		3           // Число попыток сброса датчиков температуры перед генерацией ошибки шины
#define FREQ_BASE_TIME_READ 	1000UL	// Частотные датчики - время (мсек) на котором измеряется число импульсов, в конце идет пересчет в частоту
#define MQTT_REPEAT                      // Делать попытку повторного соединения с сервером
#define MQTT_NUM_ERR_OFF   8             // Число ошибок отправки подряд при котором отключается сервис отправки MQTT (флаг сбрасывается)
#define DEFAULT_PORT_MQTT 1883           // Адрес порта сервера MQTT
#define DEFAULT_TIME_MQTT (3*60)         // период отправки на сервер в сек. 10...60000
#define DEFAULT_ADR_MQTT "mqtt.thingspeak.com"   // Адрес MQTT сервера по умолчанию
#define DEFAULT_ADR_NARMON "narodmon.ru" // Адрес сервера народного мониторинга
#define TIME_NARMON       (5*60)         // (сек) Период отправки на народный монитоинг (константа) меньше 5 минут не ставить
#define PASS_LEN          10             // Максимальная длина пароля для входа на контроллер
const char NAME_USER[]  = "user";        // имя пользователя
const char NAME_ADMIN[] = "admin";       // имя администратора
#define ATOF_ERROR       -9876543.0f     // Код ошибки преобразования строки во флоат
const char WEB_HEADER_MIME_HTML[]	= "text/html";
const char WEB_HEADER_MIME_CSS[]	= "text/css";
const char WEB_HEADER_MIME_PDF[]	= "application/pdf";
const char WEB_HEADER_OK_CT[] 			= "HTTP/1.1 200 OK\r\nAccess-Control-Allow-Origin: *\r\nContent-Type: ";
const char WEB_HEADER_TEXT_ATTACH[] 	= "text/plain\r\nContent-Disposition: attachment; filename=\"";
const char WEB_HEADER_BIN_ATTACH[] 		= "application/x-binary\r\nContent-Disposition: attachment; filename=\"";
const char WEB_HEADER_TXT_KEEP[] 		= "text/html\r\nConnection: keep-alive";
const char WEB_HEADER_END[]				= "\r\n\r\n";
const char* HEADER_FILE_NOT_FOUND = {"HTTP/1.1 404 Not Found\r\n\r\n<html>\r\n<head><title>404 NOT FOUND</title><meta charset=\"utf-8\" /></head>\r\n<body><h1>404 NOT FOUND</h1></body>\r\n</html>\r\n\r\n"};
const char* HEADER_FILE_WEB_1     = {"HTTP/1.1 200 OK\r\nContent-Type: "};
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

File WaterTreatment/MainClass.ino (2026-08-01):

/*
 * Copyright (c) 2020-2022 by Vadim Kulakov vad7@yahoo.com, vad711
 *
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
 * This file is distributed in the hope that it will be useful,
 * but WITHOUT ANY WARRANTY; without even the implied warranty of
 * MERCHANTABILITY or FITNESS FOR A PARTICULAR PURPOSE.See the
 * GNU General Public License for more details.
 */
// --------------------------------------------------------------------------------
// Описание базового класса для работы
// --------------------------------------------------------------------------------
#include "MainClass.h"

/* structsize
  char checker(int);
  char checkSizeOfInt1[sizeof(MC.Option.DailySwitch)]={checker(&checkSizeOfInt1)};
  char checkSizeOfInt1[sizeof(MC.WorkStats)]={checker(&checkSizeOfInt1)};
//*/

// Установка критической ошибки, Возвращает ошибку останова, если nam == NULL короткая запись в лог.
int8_t set_Error(int8_t _err, char *nam)
{
	if(MC.error != _err) {
		MC.error = _err;
		if(nam) strncpy(MC.source_error, nam, sizeof(MC.source_error)-1);
		m_snprintf(MC.note_error, sizeof(MC.note_error), "%s %s: %s", NowTimeToStr(), nam != NULL ? nam : "", noteError[abs(_err)]);
		if(_err == ERR_SEPTIC_PUMP_DRAIN_RUN || _err == ERR_SEPTIC_PUMP_OVERLOAD) {
			size_t _len = strlen(MC.note_error);
			m_snprintf(MC.note_error + _len, sizeof(MC.note_error) - _len - 1, "- %.3dA", SepticPower);
		} else if(_err == ERR_DRAIN_PUMP_DRAIN_RUN || _err == ERR_DRAIN_PUMP_OVERLOAD) {
			size_t _len = strlen(MC.note_error);
			m_snprintf(MC.note_error + _len, sizeof(MC.note_error) - _len - 1, "- %.3dA", DrainPumpPower);
		} else if(_err == ERR_TANK_NO_FILLING) {
			size_t _len = strlen(MC.note_error);
			m_snprintf(MC.note_error + _len, sizeof(MC.note_error) - _len - 1, "- %.2d%% за %d сек", MC.sADC[LTANK].get_Value() - FillingTankLastLevel, MC.Option.FillingTankTimeout);
		}
	}
	uint32_t i = Get_Errors_IndexEnd(_err);
	if(i != ERRORS_ARR_SIZE) {
		Errors[i] = _err;
		ErrorsTime[i] = rtcSAM3X8.unixtime();
		if(nam) {
			journal.jprintf_date("$ERROR source: %s, code: %d (0x%X)\n", nam, _err, CriticalErrors);
			if(xTaskGetSchedulerState() == taskSCHEDULER_RUNNING) {
				journal.jprintf(" State:");
				for(i = 0; i < RNUMBER; i++) journal.jprintf(" %s:%d", MC.dRelay[i].get_name(), MC.dRelay[i].get_Relay());
				for(i = 0; i < INUMBER; i++) if(MC.sInput[i].get_present()) journal.jprintf(" %s:%d", MC.sInput[i].get_name(), MC.sInput[i].get_Input());
				journal.jprintf("\n I:%.3d", MC.dPWM.get_Current());
#ifdef CHECK_DRAIN_PUMP
				journal.jprintf(",%.3d", DrainPumpPower);
#endif
#ifdef CHECK_SEPTIC
				journal.jprintf(",%.3d", SepticPower);
#endif
				for(i = 0; i < ANUMBER; i++) if(MC.sADC[i].get_present()) journal.jprintf(" %s:%.2d", MC.sADC[i].get_name(), MC.sADC[i].get_Value());
				for(i = 0; i < TNUMBER; i++) if(MC.sTemp[i].get_present()) journal.jprintf(" %s:%.2d", MC.sTemp[i].get_name(), MC.sTemp[i].get_Temp());
				journal.jprintf(" Weight:%.2d%%", Weight_Percent);
				if(_err == ERR_WEIGHT_LOW) {
					journal.jprintf("(%.1d=%d) [", Weight_value, Weight_adc_sum / (Weight_adc_flagFull ? WEIGHT_AVERAGE_BUFFER : Weight_adc_idx));
					for(i = 0; i < WEIGHT_AVERAGE_BUFFER; i++) journal.jprintf("%d,", Weight_adc_filter[i]);
					journal.jprintf("] %d", Weight_adc_idx);
				} else if(_err == ERR_PWM_DRY_RUN || _err == ERR_PWM_MAX) {
					journal.jprintf(" WBTime:%d", WaterBoosterTimeout);

				}
				journal.jprintf("\n");
			}
		} else journal.jprintf_date("$ERROR code: %d (0x%X)\n", _err, CriticalErrors);
		if(i > 0 && ErrorsTime[i] - LastErrorsClearManual < 60 * 2)	Error_Beep_confirmed = true;// Убрать звук и не посылать ошибку, если прошло меньше 2х минут после очистки ошибок.
		else MC.message.setMessage(pMESSAGE_ERROR, MC.note_error, 0);    // сформировать уведомление об ошибке
	}
	return _err;
}

// Возврат номера свободного места в массиве ошибок или размер массива, если он переполнен или ошибка уже в нем есть
uint32_t Get_Errors_IndexEnd(int8_t _err)
{
	uint32_t i = 0;
	for(; i < ERRORS_ARR_SIZE; i++) {
		if(Errors[i] == OK) break;
		if(Errors[i] == _err) {
			i = ERRORS_ARR_SIZE;
			break;
		}
	}
	return i;
}

// Стереть последнюю ошибку
void MainClass::clear_error()
{
	if(!CriticalErrors) {
		strcpy(note_error, "OK");			// Строка c описанием ошибки
		source_error[0] = '\0';				// Источник ошибки
		error = OK;                         // Код ошибки
	}
}

// стереть все ошибки
void MainClass::clear_all_errors()
{
	for(int i = 0; i < ERRORS_ARR_SIZE; i++) {
		if(error == ERR_SALT_FINISH) {
			MC.WorkStats.RegenSofteningCntAlarm = MC.Option.RegenSofteningCntAlarm;
			NeedSaveWorkStats = 1;
#if defined(CHECK_DRAIN_PUMP) && !defined(MODBUS_DRAIN_PUMP_ON_PULSE)
		} else if(error == ERR_DRAIN_PUMP_TOOLONG || error == ERR_DRAIN_PUMP_OVERLOAD || error == ERR_DRAIN_PUMP_DRAIN_RUN) {
			DrainPumpRelayStatus = MODBUS_RELAY_CMD_ON;
#endif
#if defined(CHECK_SEPTIC) && !defined(MODBUS_SEPTIC_PUMP_ON_PULSE)
		} else if(error == ERR_SEPTIC_PUMP_TOOLONG || error == ERR_SEPTIC_PUMP_OVERLOAD || error == ERR_SEPTIC_PUMP_DRAIN_RUN) {
			SepticPumpRelayStatus = MODBUS_RELAY_CMD_ON;
#endif
		} else if(error == ERR_SEPTIC_PUMP_NOT_WORK) {
			UsedWaterToSeptic = 0;
#if !defined(MODBUS_SEPTIC_PUMP_ON_PULSE)
			SepticPumpRelayStatus = MODBUS_RELAY_CMD_ON;
#endif
		} else if(error == ERR_WATER_CNT_FAIL) {
			WaterBoosterFlag = 0;
		}
	}
	memset(Errors, 0, sizeof(Errors));
	memset(ErrorsTime, 0, sizeof(ErrorsTime));
	CriticalErrors = 0;
	MC.clear_error();
	// Water ON
	if(!(MC.RTC_store.Work & (RTC_Work_Regen_F1 | RTC_Work_Regen_F2))) {
		MC.dRelay[RWATEROFF1].set_OFF();
		MC.dRelay[RWATERON].set_ON();
	}
}

// сбросить счетчик фильтра, после нужно вызвать сохранение настроек!
bool MainClass::clear_filter_counter(char *str)
{
	int32_t l_i32 = 0;
	if(strcmp(str, "RO1") == 0) {	// RESET_CNT_FCRO1
		l_i32 = MC.WorkStats.RO_FilterCounter1 * 10;
		MC.WorkStats.RO_FilterCounter1 = 0;
		MC.Option.RO_FilterCountersResetTime[0] = rtcSAM3X8.unixtime();
	} else if(strcmp(str, "RO2") == 0) {	// RESET_CNT_FCRO2
		l_i32 = MC.WorkStats.RO_FilterCounter2 * 10;
		MC.WorkStats.RO_FilterCounter2 = 0;
		MC.Option.RO_FilterCountersResetTime[1] = rtcSAM3X8.unixtime();
	} else if(strcmp(str, "1") == 0) {	// RESET_CNT_FC1
		l_i32 = MC.WorkStats.FilterCounter1 * 100;
		MC.WorkStats.FilterCounter1 = 0;
		MC.Option.FilterCountersResetTime[0] = rtcSAM3X8.unixtime();
	} else if(strcmp(str, "2") == 0) {	// RESET_CNT_FC2
		l_i32 = MC.WorkStats.FilterCounter2 * 100;
		MC.WorkStats.FilterCounter2 = 0;
		MC.Option.FilterCountersResetTime[1] = rtcSAM3X8.unixtime();
	} else return false;
	journal.jprintf_date("RESET FILTER CNT: %s at %dL\n", str, l_i32);
	NeedSaveWorkStats = 1;
	return true;
}

void Weight_Clear_Averaging(void)
{
	memset(Weight_adc_filter, 0, sizeof(Weight_adc_filter));
	Weight_adc_sum = 0;
	Weight_adc_flagFull = false;
	Weight_adc_idx = 0;
}

// Read successfully - true
bool Weight_Read(bool skip_error)
{
//		if(Weight_NeedRead) { // allways
			if(MC.get_testMode() != NORMAL) {
//				Weight_NeedRead = false;
				if(Weight_value != Weight_Test) {
					Weight_value = Weight_Test;
					Weight_Percent = Weight_value * 1000 / MC.Option.WeightFull;
				}
			} else if(Weight.is_ready()) { // 10Hz or 80Hz
//				Weight_NeedRead = false;
				// Read HX711
				int32_t adc_val, median3 = Weight.read();
				if(median3 < MC.Option.WeightZero) {
					if(Weight_Wrong_ADC_Cnt < WEIGHT_SKIP_WRONG_ADC_NUM) {
						Weight_Wrong_ADC_Cnt++;
						return false;
					}
				} else Weight_Wrong_ADC_Cnt = 0;
				// Медианный фильтр
				if(Weight_adc_median1 <= Weight_adc_median2 && Weight_adc_median1 <= median3) {
					adc_val = Weight_adc_median2 <= median3 ? Weight_adc_median2 : median3;
				} else if(Weight_adc_median2 <= Weight_adc_median1 && Weight_adc_median2 <= median3) {
					adc_val = Weight_adc_median1 <= median3 ? Weight_adc_median1 : median3;
				} else {
					adc_val = Weight_adc_median1 <= Weight_adc_median2 ? Weight_adc_median1 : Weight_adc_median2;
				}
				Weight_adc_median1 = Weight_adc_median2;
				Weight_adc_median2 = median3;
//				if(GETBIT(MC.Option.flags, fDebugToSerial)) journal.printf("HX711[%u]: %d=%d", GetTickCount(), median3, adc_val);
				// Усреднение значений
				Weight_adc_sum = Weight_adc_sum + adc_val - Weight_adc_filter[Weight_adc_idx];
				Weight_adc_filter[Weight_adc_idx] = adc_val;
				if(Weight_adc_idx < WEIGHT_AVERAGE_BUFFER - 1) Weight_adc_idx++;
				else {
					Weight_adc_idx = 0;
					Weight_adc_flagFull = true;
				}
				if(Weight_adc_flagFull) adc_val = Weight_adc_sum / WEIGHT_AVERAGE_BUFFER; else adc_val = Weight_adc_sum / Weight_adc_idx;
//				if(GETBIT(MC.Option.flags, fDebugToSerial)) journal.printf("=%d\n", adc_val);
				Weight_value = (int64_t)(adc_val - MC.Option.WeightZero) * 10000 / MC.Option.WeightScale - MC.Option.WeightTare;
				Weight_Percent = Weight_value * 1000 / MC.Option.WeightFull;
				if(Weight_Percent < 0) Weight_Percent = 0; else if(Weight_Percent > 10000) Weight_Percent = 10000;
				if(!skip_error) {
					if(Weight_Percent < MC.Option.Weight_Low) {
						if(!(CriticalErrors & ERRC_WeightEmpty)) {
							if(Weight_Percent <= 10) {
								CriticalErrors |= ERRC_WeightEmpty;
								set_Error(ERR_WEIGHT_EMPTY, (char*)__FUNCTION__);
							} else set_Error(ERR_WEIGHT_LOW, (char*)__FUNCTION__);
						}
					} else if(CriticalErrors & ERRC_WeightEmpty) CriticalErrors &= ~ERRC_WeightEmpty;
				}
				return true;
			}
//		}
		return false;
}

void MainClass::init()
{
	int i;
	clear_error();
	memset(&DailySwitchTimerCnt, 0, sizeof(DailySwitchTimerCnt));

	for(i = 0; i < TNUMBER; i++) sTemp[i].initTemp(i);            // Инициализация датчиков температуры

	for(i = 0; i < ANUMBER; i++) sADC[i].initSensorADC(i, pinsAnalog[i], ADC_FILTER[i]);	// Инициализация аналогового датчика

	for(i = 0; i < INUMBER; i++) sInput[i].initInput(i);           // Инициализация контактных датчиков
	for(i = 0; i < FNUMBER; i++) sFrequency[i].initFrequency(i);  // Инициализация частотных датчиков
	for(i = 0; i < RNUMBER; i++) dRelay[i].initRelay(i);           // Инициализация реле

	dRelay[RWATERON].set_ON();

	dPWM.initPWM();                                           // инициализация счетчика
	message.initMessage(MAIN_WEB_TASK);                       // Инициализация Уведомлений, параметр - номер потока сервера в котором идет отправка
#ifdef MQTT
	clMQTT.initMQTT(MAIN_WEB_TASK);                           // Инициализация MQTT, параметр - номер потока сервера в котором идет отправка
#endif

	ChartWaterBoost.init();
	ChartFeedPump.init();
	ChartFillTank.init();
	ChartBrineWeight.init();
	ChartWaterBoosterCount.init();
#ifdef CHECK_DRAIN_PUMP
	ChartDrainPump.init();
#endif
#ifdef CHECK_SEPTIC
	ChartSepticPump.init();
#endif

	resetSetting();                                           // все переменные
}

// Получить число ошибок чтения ВСЕХ датчиков темпеартуры
uint32_t MainClass::get_errorReadTemp()
{
	uint32_t sum = 0;
	for(uint8_t i = 0; i < TNUMBER; i++) sum += sTemp[i].get_sumErrorRead();     // Суммирование ошибок по всем датчикам
	return sum;
}

void MainClass::Reset_TempErrors()
{
	for(uint8_t i=0; i<TNUMBER; i++) sTemp[i].Reset_Errors();
}

// возвращает строку с найденными датчиками
void MainClass::scan_OneWire(char *result_str)
{
	if(!OW_scan_flags && OW_prepare_buffers()) {
		OW_scan_flags = 1; // Идет сканирование
		journal.jprintf("Scan 1-Wire:\n");
//		char *_result_str = result_str + m_strlen(result_str);
		OneWireBus.Scan(result_str);
#ifdef ONEWIRE_DS2482_SECOND
		OneWireBus2.Scan(result_str);
#endif
#ifdef ONEWIRE_DS2482_THIRD
		OneWireBus3.Scan(result_str);
#endif
//#ifdef ONEWIRE_DS2482_FOURTH
//		OneWireBus4.Scan(result_str);
//#endif
		journal.jprintf("Found: %d\n", OW_scanTableIdx);
//		while(strlen(_result_str)) {
//			journal.jprintf(_result_str);
//			uint16_t l = strlen(_result_str);
//			_result_str += l > PRINTF_BUF-1 ? PRINTF_BUF-1 : l;
//		}
#ifdef RADIO_SENSORS
		journal.jprintf("Radio found(%d): ", radio_received_num);
		for(uint8_t i = 0; i < radio_received_num; i++) {
			OW_scanTable[OW_scanTableIdx].num = OW_scanTableIdx + 1;
			OW_scanTable[OW_scanTableIdx].bus = 7;
			memset(&OW_scanTable[OW_scanTableIdx].address, 0, sizeof(OW_scanTable[0].address));
			OW_scanTable[OW_scanTableIdx].address[0] = tRadio;
			memcpy(&OW_scanTable[OW_scanTableIdx].address[1], &radio_received[i].serial_num, sizeof(radio_received[0].serial_num));
			char *p = result_str + strlen(result_str);
			m_snprintf(p, 64, "%d:RADIO %.1fV/%c:%.2f:%u:7;", OW_scanTable[OW_scanTableIdx].num, (float)radio_received[i].battery/10, Radio_RSSI_to_Level(radio_received[i].RSSI), (float)radio_received[i].Temp/100.0, radio_received[i].serial_num);
			journal.jprintf("%s", p);
			if(++OW_scanTableIdx >= OW_scanTable_max) break;
		}
		journal.jprintf("\n");
#endif
		OW_scan_flags = 0;
	}
}

// Установить синхронизацию по NTP
void MainClass::set_updateNTP(boolean b)
{
	if (b) SETBIT1(DateTime.flags,fUpdateNTP); else SETBIT0(DateTime.flags,fUpdateNTP);
}

// Получить флаг возможности синхронизации по NTP
boolean MainClass::get_updateNTP()
{
  return GETBIT(DateTime.flags,fUpdateNTP);
}

// Получить источник загрузки веб морды
TYPE_SOURSE_WEB MainClass::get_SourceWeb()
{
	if(get_WebStoreOnSPIFlash()) {
		switch (get_fSPIFlash())
		{
		case 0:
			if(get_fSD() == 2) return pSD_WEB;
			break;
		case 2:
			return pFLASH_WEB;
		}
		return pMIN_WEB;
	} else {
		switch (get_fSD())
		{
		case 0:
			if(get_fSPIFlash() == 2) return pFLASH_WEB;
			break;
		case 2:
			return pSD_WEB;
		}
		return pMIN_WEB;
	}
}

// Установить значение текущий режим работы
void MainClass::set_testMode(TEST_MODE b)
{
	int i;
	for(i = 0; i < TNUMBER; i++) sTemp[i].set_testMode(b);         // датчики температуры
	for(i = 0; i < ANUMBER; i++) sADC[i].set_testMode(b);          // Датчик давления
	for(i = 0; i < INUMBER; i++) sInput[i].set_testMode(b);        // Датчики сухой контакт
	for(i = 0; i < RNUMBER; i++) dRelay[i].set_testMode(b);        // Реле
#ifndef TEST_BOARD
	if(testMode > STAT_TEST && b <= STAT_TEST) {
		MC.load_WorkStats();
		if(rtcI2C.readRTC(RTC_STORE_ADDR, (uint8_t*)&MC.RTC_store, sizeof(MC.RTC_store))) {
			memset(&MC.RTC_store, 0, sizeof(MC.RTC_store));
			journal.jprintf(" Error read RTC store!\n");
		}
		Stats_WaterUsed_work = 0;
		Stats_WaterRegen_work = 0;
		Stats_FeedPump_work = 0;
		Stats_WaterBooster_work = 0;
		History_WaterUsed_work = 0;
		History_WaterRegen_work = 0;
		History_FeedPump_work = 0;
		History_WaterBooster_work = 0;
		History_BoosterCountL = -1;
		Charts_WaterBooster_work = 0;
		Charts_FeedPump_work = 0;
		Charts_FillTank_work = 0;
	}
#endif
	testMode = b;
	// новый режим начинаем без ошибок
	clear_error();
}

// -------------------------------------------------------------------------
// СОХРАНЕНИЕ ВОССТАНОВЛЕНИЕ  ----------------------------------------------
// -------------------------------------------------------------------------
// РАБОТА с НАСТРОЙКАМИ  -----------------------------------------------------
// Записать настройки в память i2c: <size all><Option><DateTime><Network><message><dFC> <TYPE_sTemp><sTemp[TNUMBER]><TYPE_sADC><sADC[ANUMBER]><TYPE_sInput><sInput[INUMBER]>...<0x0000><CRC16>
// старотвый адрес I2C_SETTING_EEPROM
// Возвращает ошибку или число записанных байт
int32_t MainClass::save(void)
{
	uint16_t crc = 0xFFFF;
	uint32_t addr = I2C_SETTING_EEPROM + 2; // +size all
	uint8_t tasks_suspended = TaskSuspendAll(); // Запрет других задач
	if(error == ERR_SAVE_EEPROM || error == ERR_LOAD_EEPROM || error == ERR_CRC16_EEPROM) error = OK;
	DateTime.saveTime = rtcSAM3X8.unixtime();   // запомнить время сохранения настроек
	journal.jprintfopt("Save settings ");
	while(1) {
		// Сохранить параметры и опции отопления и бойлер, уведомления
		Option.ver = VER_SAVE;
		if(save_struct(addr, (uint8_t *) &Option, sizeof(Option), crc)) break;
		if(save_struct(addr, (uint8_t *) &DateTime, sizeof(DateTime), crc)) break;
		if(save_struct(addr, (uint8_t *) &Network, sizeof(Network), crc)) break;
		if(save_struct(addr, message.get_save_addr(), message.get_save_size(), crc)) break;
		// Сохранение отдельных объектов 
		if(save_2bytes(addr, SAVE_TYPE_sTemp, crc)) break;
		for(uint8_t i = 0; i < TNUMBER; i++) if(save_struct(addr, sTemp[i].get_save_addr(), sTemp[i].get_save_size(), crc)) break; // Сохранение датчиков температуры
		if(error == ERR_SAVE_EEPROM) break;
		if(save_2bytes(addr, SAVE_TYPE_sADC, crc)) break;
		for(uint8_t i = 0; i < ANUMBER; i++) if(save_struct(addr, sADC[i].get_save_addr(), sADC[i].get_save_size(), crc)) break; // Сохранение датчика давления
		if(error == ERR_SAVE_EEPROM) break;
		if(save_2bytes(addr, SAVE_TYPE_sInput, crc)) break;
		for(uint8_t i = 0; i < INUMBER; i++) if(save_struct(addr, sInput[i].get_save_addr(), sInput[i].get_save_size(), crc)) break; // Сохранение контактных датчиков
		if(error == ERR_SAVE_EEPROM) break;
		if(save_2bytes(addr, SAVE_TYPE_sFrequency, crc)) break;
		for(uint8_t i = 0; i < FNUMBER; i++) if(save_struct(addr, sFrequency[i].get_save_addr(), sFrequency[i].get_save_size(), crc)) break; // Сохранение контактных датчиков
		if(error == ERR_SAVE_EEPROM) break;
		#ifdef MQTT
		if(save_2bytes(addr, SAVE_TYPE_clMQTT, crc)) break;
		if(save_struct(addr, clMQTT.get_save_addr(), clMQTT.get_save_size(), crc)) break; // Сохранение MQTT
		#endif
		#ifdef CORRECT_POWER220
		if(save_2bytes(addr, SAVE_TYPE_PwrCorr, crc)) break;
		if(save_struct(addr, (uint8_t*)&correct_power220, sizeof(correct_power220), crc)) break; // Сохранение correct_power220
		#endif
		if(save_2bytes(addr, SAVE_TYPE_END, crc)) break;
		if(writeEEPROM_I2C(addr, (uint8_t *) &crc, sizeof(crc))) { error = ERR_SAVE_EEPROM; break; } // CRC
		addr = addr + sizeof(crc) - (I2C_SETTING_EEPROM + 2);
		if(writeEEPROM_I2C(I2C_SETTING_EEPROM, (uint8_t *) &addr, 2)) { error = ERR_SAVE_EEPROM; break; } // size all
		int8_t _err;
		if((_err = check_crc16_eeprom(I2C_SETTING_EEPROM + 2, addr - 2)) != OK) {
			error = _err;
			journal.jprintfopt("- Verify Error!\n");
			break;
		}
		addr += 2;
		journal.jprintfopt("OK, wrote: %d bytes, crc: %04x\n", addr, crc);
		break;
	}
	if(tasks_suspended) xTaskResumeAll(); // Разрешение других задач

	if(error == ERR_SAVE_EEPROM || error == ERR_LOAD_EEPROM || error == ERR_CRC16_EEPROM) {
		set_Error(error, (char*)__FUNCTION__);
		return error;
	}
	// суммарное число байт
	return addr;
}

// Считать настройки из памяти i2c или из RAM, если не NULL, на выходе длина или код ошибки (меньше нуля)
int32_t MainClass::load(uint8_t *buffer, uint8_t from_RAM)
{
	uint16_t size;
	journal.jprintfopt(" Load settings ");
	if(from_RAM == 0) {
		if(readEEPROM_I2C(I2C_SETTING_EEPROM, (byte*) &size, sizeof(size))) {
x_ReadError:
			error = ERR_CRC16_EEPROM;
x_Error:
			journal.jprintf(" I2C - read error %d!\n", error);
			return error;
		}
		if(size > I2C_SETTING_EEPROM_NEXT - I2C_SETTING_EEPROM) { error = ERR_BAD_LEN_EEPROM; goto x_Error; }
		if(readEEPROM_I2C(I2C_SETTING_EEPROM + sizeof(size), buffer, size)) goto x_ReadError;
	} else {
		journal.jprintfopt("FILE");
		size = *((uint16_t *) buffer);
		buffer += sizeof(size);
	}
	journal.jprintfopt(", size %d, crc: ", size + 2); // sizeof(crc)
	size -= 2;
	#ifdef LOAD_VERIFICATION
	
	uint16_t crc = 0xFFFF;
	for(uint16_t i = 0; i < size; i++)  crc = _crc16(crc, buffer[i]);
	if(crc != *((uint16_t *)(buffer + size))) {
		journal.jprintf("I2C Error: %04x != %04x!\n", crc, *((uint16_t *)(buffer + size)));
		return error = ERR_CRC16_EEPROM;
	}
	journal.jprintfopt("%04x", crc);
	#else
	journal.jprintfopt("*No verification");
	#endif
	uint8_t *buffer_max = buffer + size;
	size += 2;
	load_struct(&Option, &buffer, sizeof(Option));
	journal.jprintfopt(", v.%d ", Option.ver);
	if(Option.ver > 100) {
		journal.jprintf("\nEEPROM with garbage - reseting!\n");
		resetSetting();
		return error = ERR_CRC16_EEPROM;
//	} else if(Option.ver == 16) { // Convert
//		memmove((uint8_t*)&Option.DailySwitch + 40, (uint8_t*)&Option.DailySwitch + 30, sizeof(Option) - ((uint8_t*)&Option.DailySwitch - (uint8_t*)&Option.ver) - 40);
	}
	load_struct(&DateTime, &buffer, sizeof(DateTime));
	load_struct(&Network, &buffer, sizeof(Network));
	load_struct(message.get_save_addr(), &buffer, message.get_save_size());
	int16_t type = SAVE_TYPE_LIMIT;
	while(buffer_max > buffer) { // динамические структуры
		if(*((int16_t *) buffer) <= SAVE_TYPE_END && *((int16_t *) buffer) > SAVE_TYPE_LIMIT) {
			type = *((int16_t *) buffer);
			buffer += 2;
		}
		// массивы, длина структуры должна быть меньше 128 байт, <size[1]><<number>struct>
		uint8_t n = buffer[1]; // номер элемента
		if(type == SAVE_TYPE_sTemp) { // первый в структуре идет номер датчика
			if(n < TNUMBER) { load_struct(sTemp[n].get_save_addr(), &buffer, sTemp[n].get_save_size());	sTemp[n].after_load(); } else goto xSkip;
		} else if(type == SAVE_TYPE_sADC) {
			if(n < ANUMBER) { load_struct(sADC[n].get_save_addr(), &buffer, sADC[n].get_save_size()); sADC[n].after_load(); } else goto xSkip;
		} else if(type == SAVE_TYPE_sInput) {
			if(n < INUMBER) load_struct(sInput[n].get_save_addr(), &buffer, sInput[n].get_save_size()); else goto xSkip;
		} else if(type == SAVE_TYPE_sFrequency) {
			if(n < FNUMBER) load_struct(sFrequency[n].get_save_addr(), &buffer, sFrequency[n].get_save_size()); else goto xSkip;
		// не массивы <size[1|2]><struct>
#ifdef MQTT
		} else if(type == SAVE_TYPE_clMQTT) {
			load_struct(clMQTT.get_save_addr(), &buffer, clMQTT.get_save_size());
#endif
#ifdef CORRECT_POWER220
		} else if(type == SAVE_TYPE_PwrCorr) {
			load_struct((uint8_t*)&correct_power220, &buffer, sizeof(correct_power220));
#endif
		} else if(type == SAVE_TYPE_END) {
			break;
		} else {
xSkip:		load_struct(NULL, &buffer, 0); // skip unknown type
		}
	}
	// Recalc variables
	FilterTankSquare = CalcFilterSquare(Option.FilterTank);
	FilterTankSoftenerSquare = CalcFilterSquare(Option.FilterTankSoftener);
	//
	journal.jprintfopt("OK\n");
	return size + sizeof(crc);
}
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

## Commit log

2019-10-03 Compiling only under Arduino IDE
    [BOM_DUE Core - Main board_20190808111307.csv, BOM_DUE Core - Relay board_20190808111509.csv]
2019-11-27 digital sensors, web
2019-12-30 del SENSOR_IP
2020-01-29 ADC gain thru web
2020-02-05 median filter to weight
2020-02-06 OneWire no block interrupt
2020-03-01 LCD Flow check
2020-03-06 MDK board start
2020-04-02 +датчики протечки
2020-04-06 fix water used stats
    [Constant.h, MainClass.ino, Statistics.h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]
2020-04-07 sensorin page
2020-04-07 upd web relay
2020-05-02 флаг - питание от резерва
2020-05-02 LowConsumeMode - web relay.html
2020-05-06 работа от резерва
2020-06-17 220V UPS, Septic alarm
2020-06-30 time relay
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2020-11-24 max start regen time (5 min.) to generate error
    [Config.h, Constant.h, MainClass.h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]
2020-12-17 Показывать на главной странице запланированную регенерацию
2021-02-15 fix: login access, manual regen
    [Constant.h, WaterTreatment.ino, WebServer.ino]
2021-02-17 fix web login access
    [MainClass.h, MainClass.ino, Util.ino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]
2021-03-18 relay RWATERON - after softener
2021-03-19 LCD: add RWATERON relay
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2021-06-19 reset salt tank level
    [MainClass.ino]
2021-09-01 info LED (regen & error)
    [Config.h, Constant.h, Statistics.ino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]
2021-11-27 show K in Flow check
2021-11-30 fix weight calc error
    [MainClass.h, MainClass.ino, WebServer.ino]
2021-12-22 softening reagent control value
2022-02-07 Авторасчет дозирования по производительности насоса и нужному кол-ву реагента на литр воды
2022-02-14 Дозирование при нулевом расходе воды и падении давления
    [Microswitch_cam_Autotrol_263-268_softener.stl]
2022-02-15 флаг для вкл/выкл дозирования по давлению при нулевом протоке
2022-02-21 По понижению давления при нулевом расходе корректируется расход (+...м3ч)
2022-02-28 Минимальный проток, ниже которого, начинать добавлять расход
2022-04-04 new Autotrol switch
    [Microswitch_cam_Autotrol_263-268_softener2.stl]
2022-07-16 LowConsume mode improved, fix some err
    [Config.h, Constant.h, MainClass.h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]
2022-12-27 Периодичное включение реле RFILL для вытяжного вентилятора радона
2023-10-10 skip weight value less than ADC zero settings
    [Constant.h, MainClass.ino]
2023-10-23 слив отстоя с бака
2023-11-21 проверка бака на герметичность, рефакторинг
2023-11-21 максимальное время заполнения бака, если превышено - критическая ошибка
2024-01-02 защита от открытого крана (ограничение длительного потребления)
2024-01-03 макс время непрерывного потребления (меню система), сброс по сохранению соответ. настройки
2024-01-12 редкое мигание светодиодом оповещения когда ожидается регенерация
2024-02-01 Add filter timer 1,2
2024-02-13 счетчики ресурса фильтров (2 шт)
2024-02-17 Начальный час мигания предупреждения о надвигающейся регенерации
2024-02-28 Начало доработки по контролю и отключению дренажных насосов
2024-02-29 опрос счетчика насосов через модбас, отключение насоса через модбас реле
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2024-03-03 Входной контакт - низкая температура септика
2024-03-05 add septic relay, modbus refactoring
2024-03-09 контроль работы дренажного насоса во время регенерации
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2024-03-10 минимальная мощность дренажного насоса
2024-03-31 поддержка счетчиков воды с 1 л на импульс и выше
2024-04-02 изменены графики, прибавка расхода при низком расходе считается логарифмически
2024-04-03 стартовый объем бака в настройках
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2024-04-05 еще настройка для осмоса
2024-04-19 Водосчетчик с выдачей данных по I2C шине (схема и прошивка платы водосчетчика, оптосенсор крепится над звездочкой счетчика)
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2024-05-25 Добавлена плата водосчетчика с импульсным выходом
2024-05-26 Контроль превышения мощности дренажного насоса
2024-05-27 Обновление прошивки импульсного счетчика
2024-07-30 задержка включения алгоритма при минимальном потреблении
2024-12-08 Второй счетчик на осмос. В работе...
2024-12-15 Второй счетчик на осмос. Статистика. В работе...
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2024-12-22 Проверка расхода частотных датчиков через веб
2024-12-22 Arduino hardware lib SAM patch
2024-12-22 количество емкостей *(0.5л и 1л) в калибровке
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2024-12-26 расчет датчиков протока с нелинейностью
    [Расчет датчиков протока.xlsx]
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2025-01-19 защита дренажного насоса от сухого хода
2025-01-20 График мощности дренажного насоса, период опроса его
2025-05-26 Контроль насоса септика, начало
2025-05-27 Насос септика, контроль расхода воды в септик, контроль электро-потребление всего септика
2025-06-01 Рефакторинг, исправление ошибок
2025-06-02 Реле насоса септика, возможность работы со сломаным или без поплавка насоса
2025-06-03 Отображение инфы по дренажным насосам на гл. экране
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2025-06-08 Добавлен Serial3 для Modbus с автовыбором по адресу устройства
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2025-06-11 Таймеры (ежесуточные и периодические), включение обычных реле и Modbus
2025-06-16 при аварии септика включается насос, если он был выключен
2025-07-16 Дельта уровня бака для проверки на утечку или скорость заполнения -> в десятых %
2025-08-01 отказ от семафоров RTOS
2025-08-05 автоотключение ошибки септика, возможность отключать только 1 кран при ошибке септика
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2025-08-08 контроль включения/выключения через реле насоса септика
2025-08-08 настройка реверса реле насоса септика
2025-08-08 Реверс реле насоса септика
2025-08-15 В статистике детально мощность фиксируется максимальная за минуту
2025-08-18 контроль работоспособности датчика питьевого фильтра
2025-09-02 доработка библиотеки Ethernet - функция RTOS_delay() во время ожидания
2026-01-08 add yield() to 1-wire,I2C lib
2026-01-28 ожидание отработки насоса септика после срабатывания датчика переполнения до ошибки
2026-02-22 fix septic pump
2026-02-25 Замена: контроль тока насосов вместо мощности
2026-03-07 контроль номинального потребления септика
2026-03-16 сухой ход насоса септика по разнице тока от пред.потребления
2026-04-09 Ошибка счетчика питьевого фильтра через 7 дней отсутствия потребления и наличия низкого расхода
